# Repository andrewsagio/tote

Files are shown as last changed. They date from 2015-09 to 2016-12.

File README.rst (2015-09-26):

Tote, a Small Spider Quadruped Robot
************************************

This is a small (fits in your palm) walking robot, with three degree of freedom
legs, with Ardunio (Pro Mini) for the brain and controlled by a TV remote. It
is supposed to be very simple, very cheap and very sturdy (but please don't
step on it).

See the documentation at http://tote.rtfd.org

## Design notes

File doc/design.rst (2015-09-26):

Design Decisions
****************

Design Goals and Constraints
============================

The main goal is to have a walking robot that is interesting to program and at
the same time easy to build. From that, we get a number of constraints:

    * The robot has to fit on the desk, because not everyone has a garage.
    * It has to have inverse kinematics, otherwise we are limited to replaying
      pre-recorded movements.
    * It should avoid parts that are custom-made using tools and materials that
      are not widely available. In particular, no laser-cutting or 3D-printing.
    * The parts should be common, cheap and easy to get, also in bulk.
    * It should be possible to easily extend or modify the robot.
    * In the basic version it should have enough functionality to be fun to
      play with.

Hacks and Workarounds
=====================

Because of the above constraints and the desire to make it all as cheap as
possible, I've made some design decisions that are not exactly good
engineering.  I figured out that it's better to have a crappy but working
robot, than a beautifully designed plan. So here are some corners that I've
cut:

Mechanical Design
-----------------

The way this robot is assembled together only works because it's so
lightweight. Would the robot be heavier, there would be significant problems:

    * Servomotors are used as structural elements.
    * The printed circuit board is also used as a structural element.
    * The whole robot weight rests sideways on the servo shafts.
    * The servo horns used for legs are elastic.
    * The screws that come with the servos are too big for what they used for.
    * The servo cables are all over the place.
    * The power switch is in an awkward place.
    * There is no good way to attach the battery.
    * The legs need some rubber at their ends, or they will slip.

Most of those problems can be solved by using better materials and adding some
structural support elements, but that affects the price and complexity.

Electrical Design
-----------------

The desire to cut costs and minimise the number of parts also made me make some
not-entirely-kosher decisions on the electrical side of things:

    * The servomechanisms are under-powered. The specification asks for 4.6V,
      and they get from 3.6V to 4.2V depending on the charge level of the LiPo
      battery.
    * The servomechanisms are powered directly from the battery, without any
      kind of voltage regulator.
    * The undercharge battery protection is software-based, which means it can
      easily fail.
    * There is no battery charger build in. You have to disconnect the battery
      to charge it.
    * The Pro Mini is soldered directly onto the printed circuit board.

Those problems can be easily solved by adding the missing parts to the design.
There is even some room left for them, in the form of additional holes and
pins.

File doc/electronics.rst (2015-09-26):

Electronics
===========

The designs of the main printed circuit board are available in the code
repository_. You will need Fritzing software to open them and export as
whatever format is required for fabricating it.

.. _repository: https://bitbucket.org/thesheep/tote

Arduino Pro Mini is used for the brains of the robot. It is connected directly
to the servo signals and to the battery. There is also a 1000µF electrolytic
capacitor connected across the battery to avoid brown-outs. An optional voltage
divider of two 47kΩ resistors, with a 47nF capacitor for noise reduction is
used to monitor the battery voltage and shut down the robot when it drops too
low. The battery is any light 1S, 3.7V LiPo cell. Other kinds of batteries can
be used, as long as they are light enough and provide enough power. Remote
control is done using a VS1838B infra-red sensor, but other sensors can be
used.

Several pins of the Arduino are free, including the I²C pins, allowing for
connecting more sensors.

The prototype also has an optional LiPo charging/protection module attached,
for convenience, although the battery can be charged by any suitable charger.

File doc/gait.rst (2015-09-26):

Walking Algorithms
******************

The way in which an animal or a robot walk is called a gait -- it tells us
how and in what order the legs are moved, how the body is balanced and how
it moves forward.

Statically and Dynamically Stable Gaits
=======================================

When the robot walks, it has to keep its balance. There are two general
strategies for doing that, and according to them, we divide the gaits into
statically stable and dynamically stable.

For statically stable gaits it doesn't matter how fast they are performed, or
whether the robot is stopped in a middle of a step -- it is stable at any
moment, at all times. Animals and people use those gaits when they want to go
slowly, or when they want to be able to stop at any time. An example of such a
gait is the "creep" gait, used by cats stalking their prey.

Dynamically stable gaits are much harder, as they have to be performed at a
particular speed and cannot be interrupted at an arbitrary point. They are
sometimes called "controlled falling", as they exploit the fact that it takes
some time for the robot to fall when it's unstable, and that time can be used
to move the legs in such a way as to prevent the fall. Most animal gaits are
dynamically stable, as they tend to be faster and more energy-efficient. An
example of a simple dynamically stable gait is the "trot" gait.

Area of Support
===============

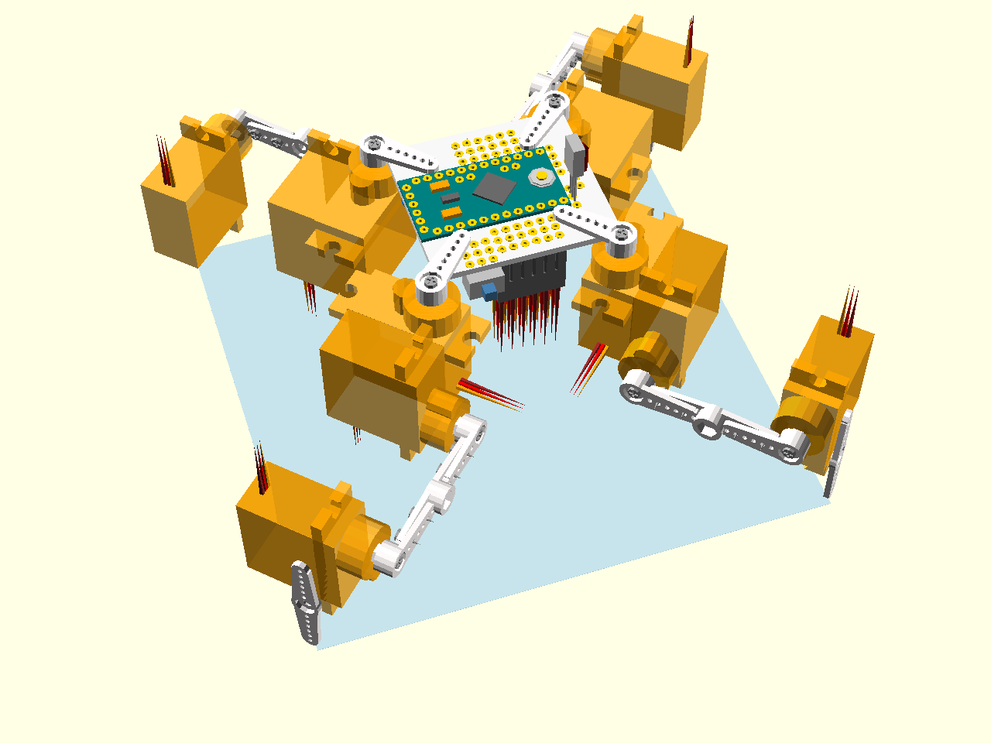
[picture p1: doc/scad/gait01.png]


I order for a relatively light robot, like ours, to be statically stable, it
has to keep its center of mass somewhere between its legs. More precisely, if
you connect all the feet on the ground with straight lines, so that they form a
convex polygon, the center of mass has to be located directly over it. We call
that polygon the "area of support" of the robot at the given moment. The area
of support will change depending on which legs are placed on the ground and
where, so the robot will sometimes need to shift its center of mass around to
remain stable while changing its stance.

The image above shows the are of support of our robot in the starting position.

In a heavier robot, you also have to take into account the inertia, so that
it's not sufficient to just track the center of mass -- you have to track the
so-called "zero-moment point", often abbreviated ZMP, which is basically the
point on the ground directly below the center of mass, shifted to account for
the inertia. We will not get into details of that here, as our robot is light
enough that just leaving some small margin around the area of support is
enough.

Raising a Leg
-------------

When the robot raises one of the legs, its area of support changes dramatically:

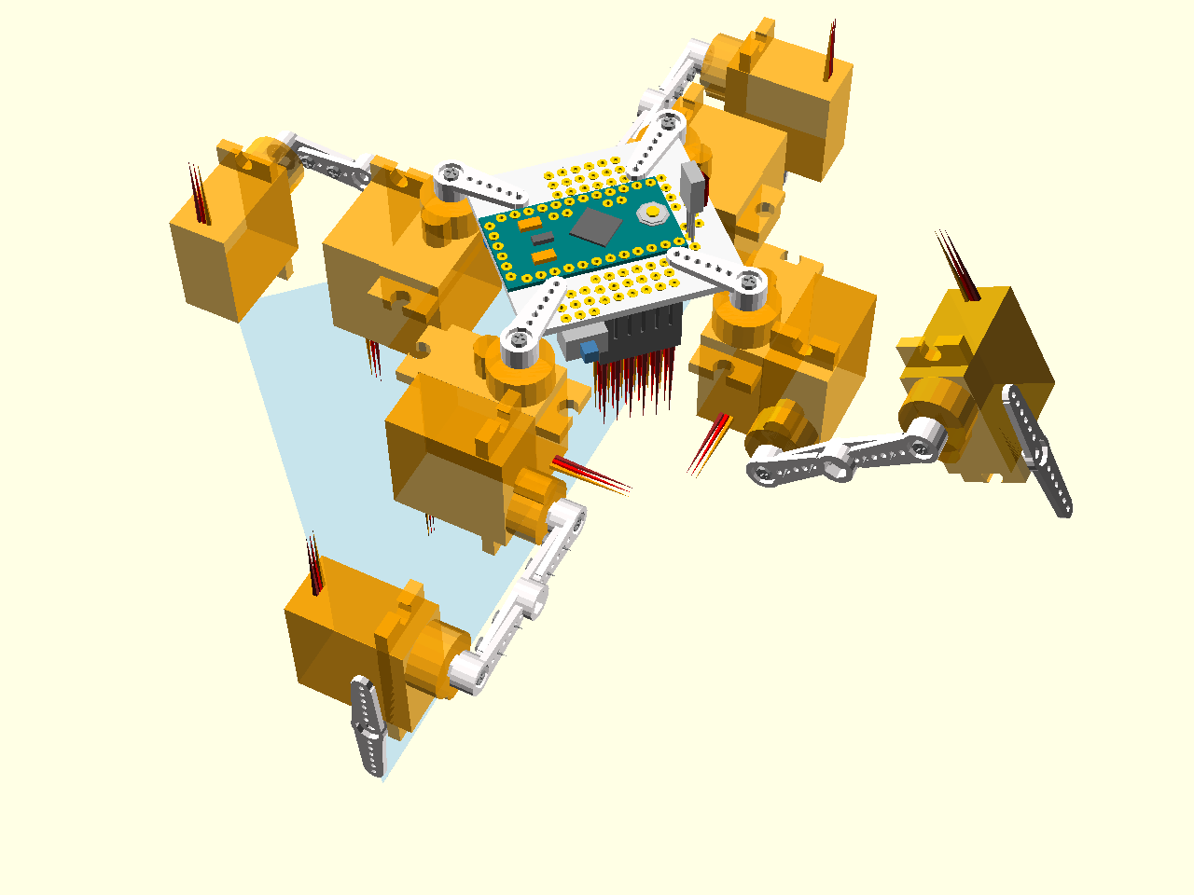
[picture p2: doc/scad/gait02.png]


You can see, that our center of mass is directly on an edge of our area of support. That's bad, because the smallest force can now tip our robot and make it fall. We can avoid that by moving all the legs toward the one leg that we want to raise before raising it, so that the center of mass shifts:

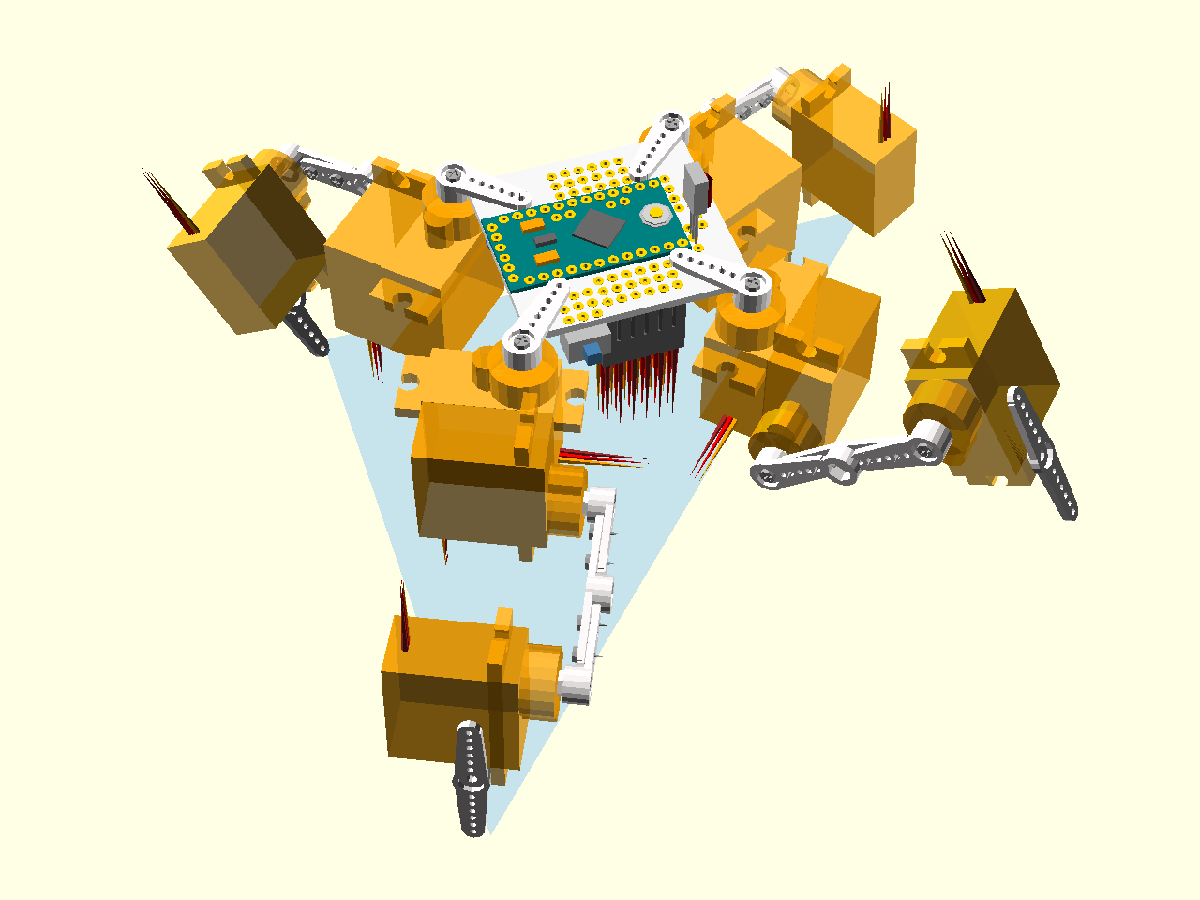
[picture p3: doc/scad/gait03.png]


There are also other methods of balancing, not covered here. For example, many
animals have a flexible spine, that they can bend sideways to shift their
center of mass. Other animals have tails that they use to balance.
Possibilities are endless.

Moving Forward
==============

Our goal is to propel our robot horizontally across the floor. The simplest
solution to do that, at least initially, is to just move all the legs that are
touching the ground backwards. If we do it slow enough, so that they don't
slip, they will stay where they were, but move the body of the robot forward.
This is an excellent way of moving around, and many industrial robots do it
this way, bolted to the floor in one place. There is however a small problem:
the range is quite limited. Sooner or later you will either move your center of
mass outside the support area, or your legs move to their maximum range. What
then?

Then you raise the legs from the ground, move them forward, and set them down
in the new place. But you have to be smart about it, because if you do it with
all the legs at once, you will fall down. But you can raise a single leg and
still stand on the remaining three. You can also raise and move that leg
*while* moving the remaining legs backwards, which saves you some time and
makes it both faster and more smooth.

Now, as you know, if you are raising a leg, you also have to make sure that the
center of mass stays inside the support area. To do that, you will have to
shift the robot's body away from the leg that you are rising. Since you are
shifting your body forwards, it is also important in which order you raise the
legs -- some orders will be more stable than others.

So, to sum, our plan of action is:
  * move all the legs that are on the ground backwards,
  * for each leg in a set order:

    + shift the body away from that leg
    + raise the leg
    + move the leg forward
    + set the leg on the ground.

The Creep Gait
==============

What order is the best for making steps, if you raise one leg at a time? There
are four possible orders, assuming you always start with the same leg, and
ignore the orders that are just reflections.

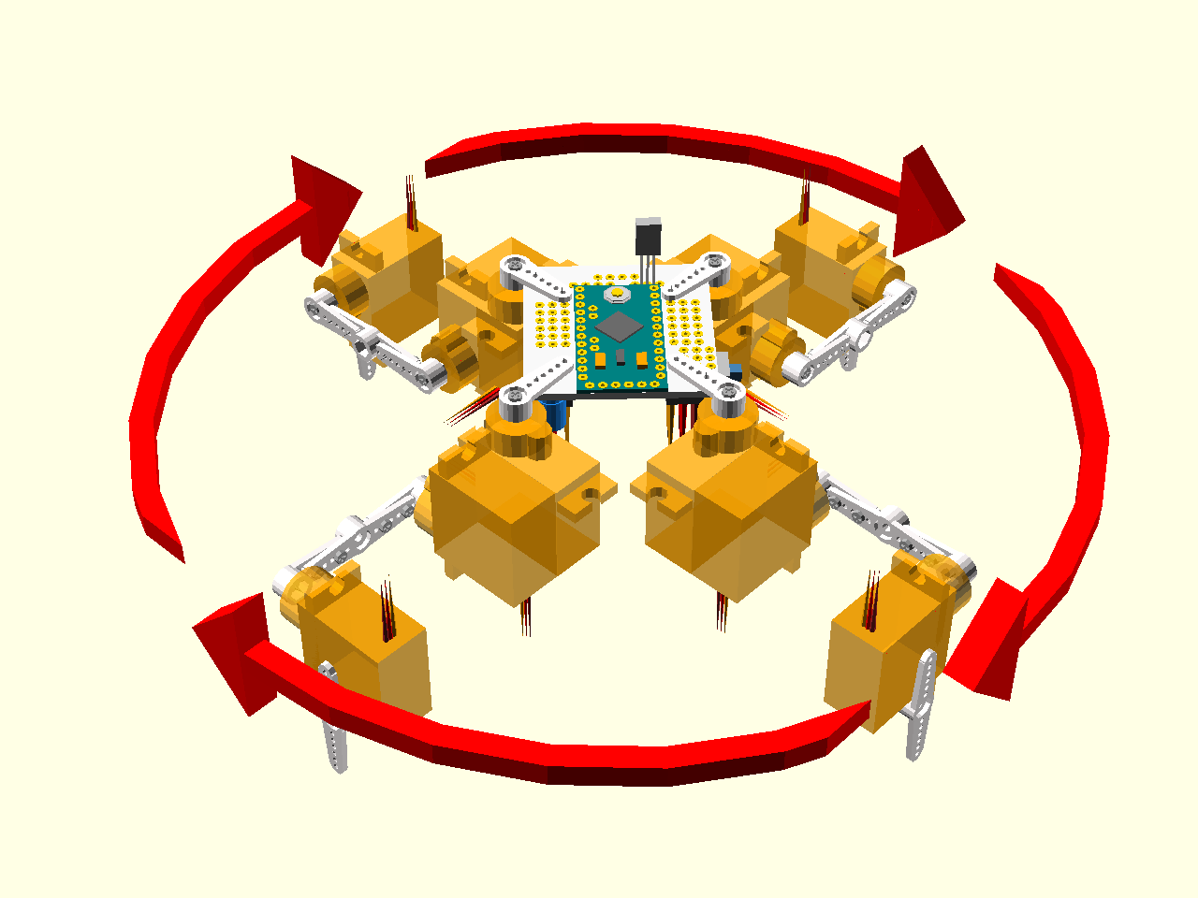
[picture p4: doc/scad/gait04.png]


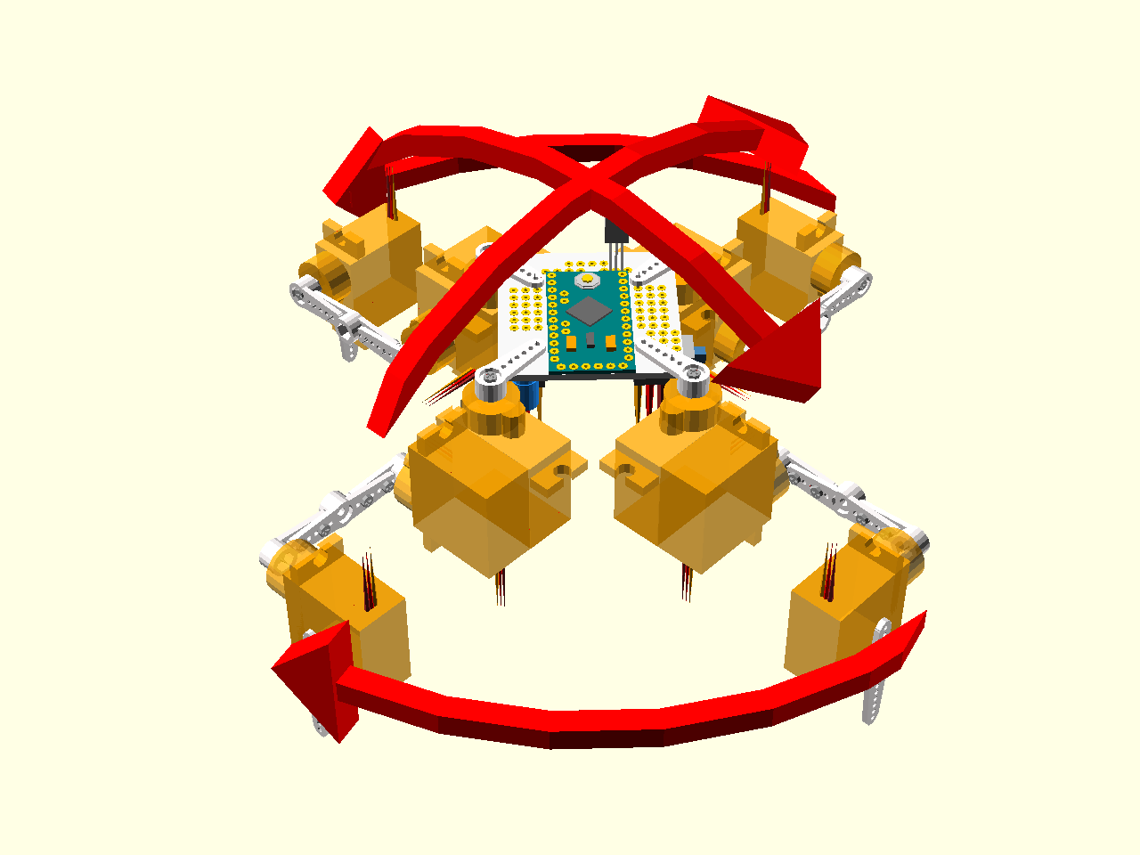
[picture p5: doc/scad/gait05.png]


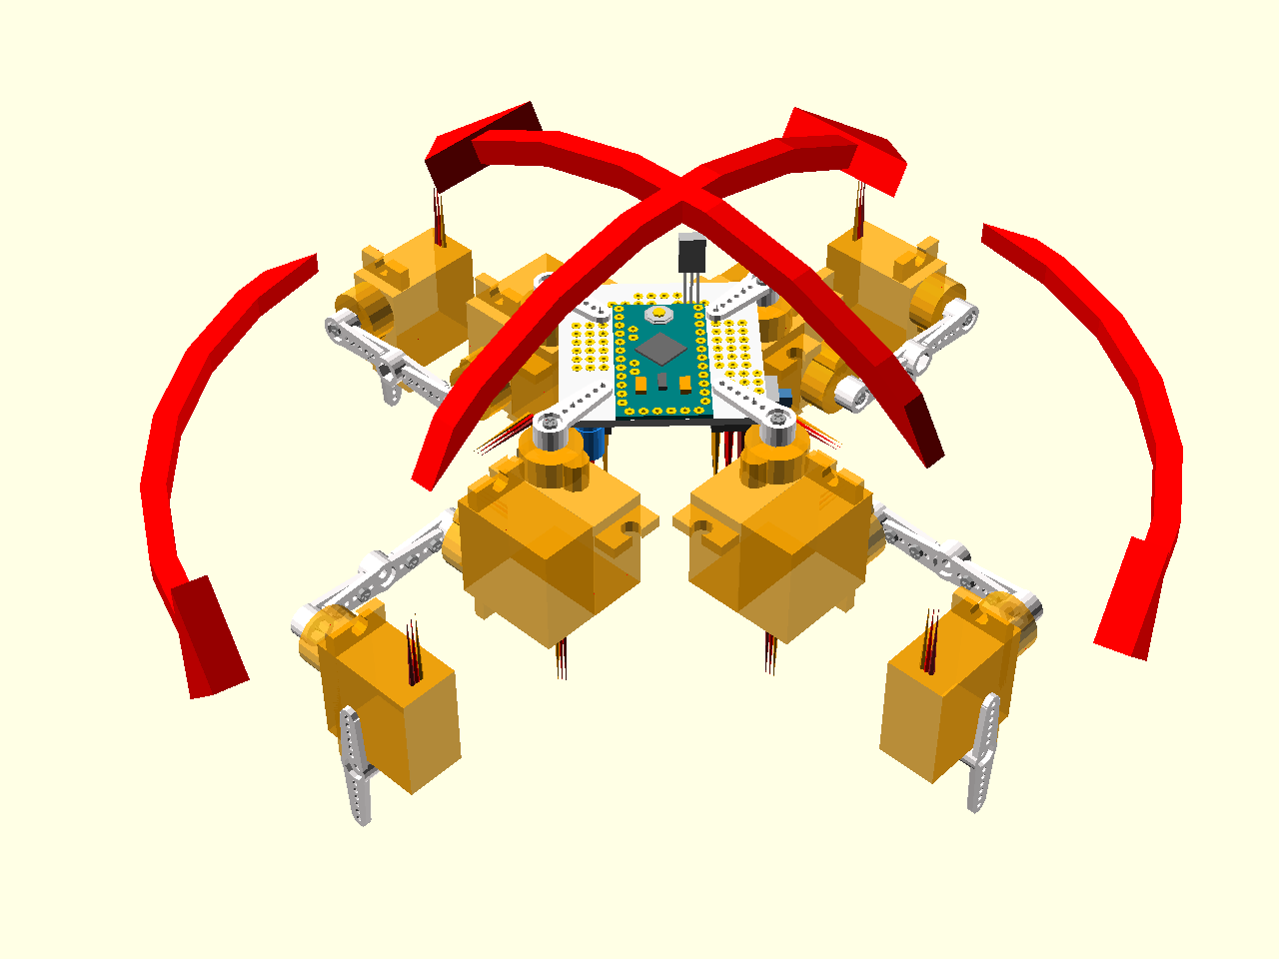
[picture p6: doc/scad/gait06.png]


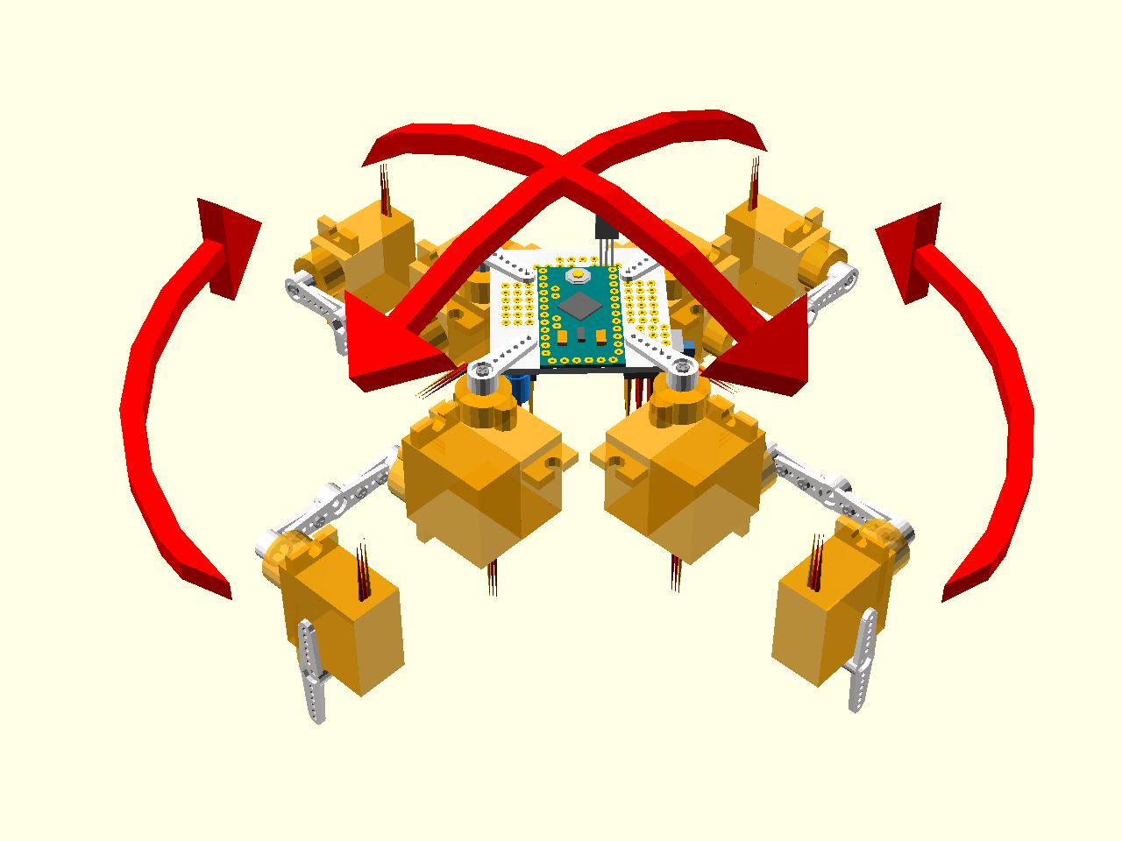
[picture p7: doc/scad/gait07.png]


Both calculations and experimental data show that the last one, a figure eight
orthogonal to the direction of walking, provides the optimal stability at all
moments.  Note that this order is best only when you are moving forward. If you
are moving sideways, backwards or rotating, then other leg orders are optimal.
That's why it probably makes sense to adapt the order to the situation.

The Trot Gait
=============

The creep gait is stable, but quite slow -- raising only one leg at a time, you
can't move the remaining legs backwards too fast, or you move out of the range
of your legs. In addition, shifting the robot's body before each step also
takes some time. Is there a faster way?

Turns out that you can move two opposite legs at the same time, if only you do
it fast enough, so that the robot will not have time to tip on the two
remaining legs. This is not a statically stable gait -- you can only stop
safely between steps, when all the legs are on the ground, but it's more than
twice as fast as the creep gait: first, you move two legs at a time, and
second, you don't have to shift your body for balance.

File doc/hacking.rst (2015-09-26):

Modifying and Extending
***********************

Since this robot is so simple, it is very easy to modify or extend it. You can
add sensors and peripherals, or control it remotely from another computer or
directly with another microcontroller or microcomputer board.

GPIO Pins
---------

Most of the Arduino's pins are used internally, but there are several of them
left for your use:

  * 7 pins can be used as digital,

    - 1 of them has a LED on it,
    - 2 of them can be used as serial interface,
    - 2 of them can trigger interrupts,

      + 1 of them has PWM,

    - 2 other can be also used as analog pins,

      + they can also be used as I²C interface,

  * 2 analog-only pins.

Sensors
-------

You can connect anything that runs on 3.3V and can be connected either to the
free GPIO pins, or to additional board or multiplexer that you add. Examples
include:

  * ultrasonic distance sensor, such as HC-SR04,
  * switches at the ends of the feet,
  * accelerometer, gyroscope and/or compass,
  * encoders for leg positions,
  * light sensors, for following light,

Peripherals
-----------

You can also use the GPIOs to attach additional hardware that would do
something. Unfortunately, you cannot easily add more servos, as the Arduino
Servo library being used only supports 12 of them at once. But instead you
can add:

  * piezoelectric buzzer, for beeping,
  * addressable LEDs, for light effects,
  * infrared diode, for "shooting" at other robots in a laser-tag game,
  * a nerf gun,
  * a LiPo battery charger.

Remote Control
--------------

You can use the serial interface to connect a transmitter/receiver module and
make the robot communicate with another device. For example, you can use:

  * WiFi module, such as ESP8266,
  * Bluetooth module, such as HC-05,
  * Radio module, such as NRF24,
  * BLE module,
  * and so on.

Additional Boards
-----------------

You can also add another microcontroller or microcomputer board to the robot,
and make it communicate with it either through the serial or I²C pins. Some
examples include:

  * Arduino Pro Mini, with more pins,
  * VoCore, a computer running OpenWRT Linux,
  * PyBoard, a microcontroller runnning MicroPython,
  * Teensy 3.1, an ARM-based microcontroller board,
  * OpenMV, a microcomputer with a camera, programmable with Python,
  * ESP8266 with NodeMCU firmware, programmable in Lua.

The possibilities are infinite, as long as the board in question has a serial
or I²C interface, can be powered from a single LiPo battery, and doesn't weight
too much for the robot to carry it.

If your board or module can be powered with 3.3V, simply use the FTDI header of
your Pro Mini for connecting it -- it has broken out the power and serial
interface. You will have to write the code for communicating with the board
yourself.

If the board requires 5V or considerable amounts of current, you don't want to
power it from Pro Mini's power regulator. Instead, add pins to the RAW and GND
pads on it, and to the RX and TX pads:

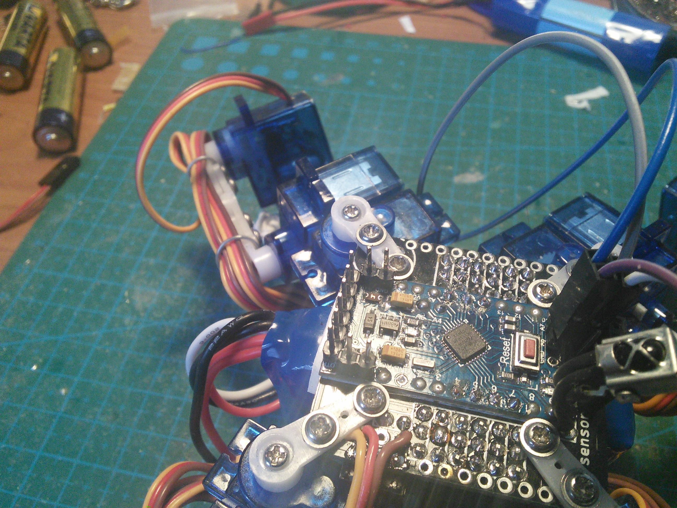
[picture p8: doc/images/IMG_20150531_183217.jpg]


Then use a double-row female header to connect your breakout board to the Pro
Mini:

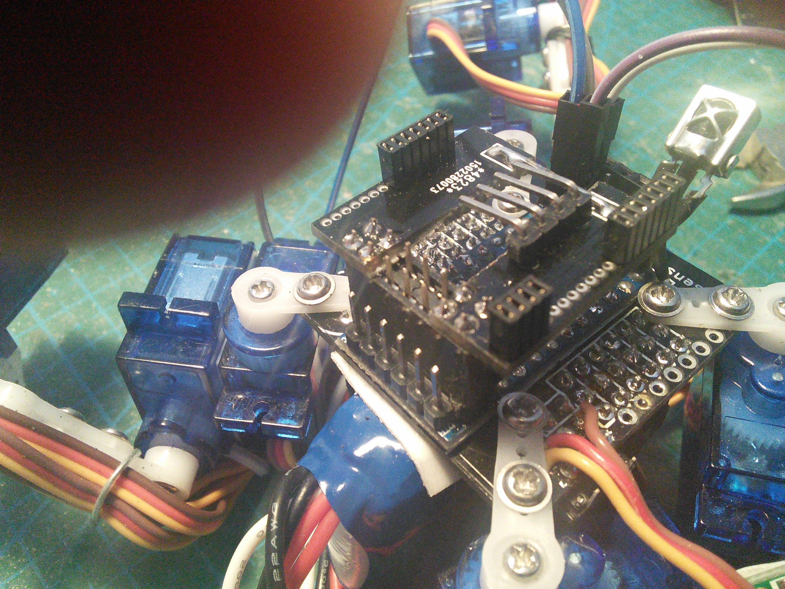
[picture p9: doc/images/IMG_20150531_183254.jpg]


And connect your board on top of that:

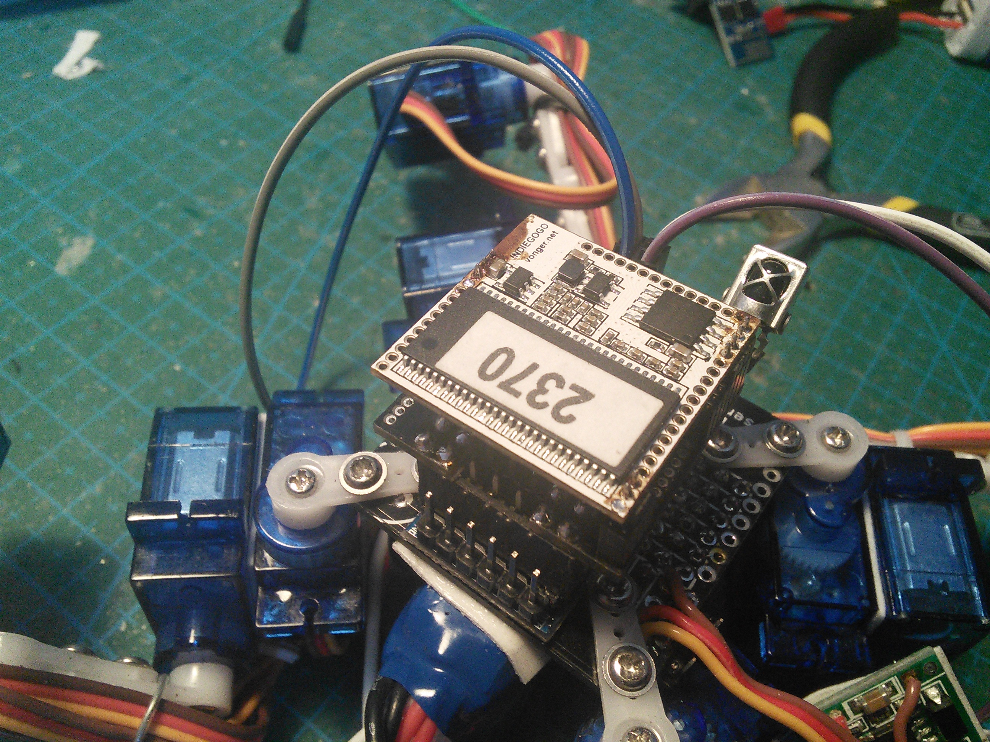
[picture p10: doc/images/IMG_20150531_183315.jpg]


Of course, you will need to use a power source that can power your board.

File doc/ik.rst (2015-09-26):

Inverse Kinematics
******************

Kinematics is the process of determining how a robot will move given certain
inputs. Inverse kinematics is for determining what inputs we need to give it to
get into a certain position. In particular, leg inverse kinematics for walking
robots is the process of calculating the angles for all the joints required to
get the tip of the leg in a certain position relative to the body. There is
also body inverse kinematics, which tells us in what positions the legs have to
be for the body to be in a certain position (tilt, yaw, rotation, shift).

This are notes for determining the inverse kinematics for a four-legged robot
with three degrees of freedom per leg. Let's start with an image of the leg:

Basic Trigonometry
==================

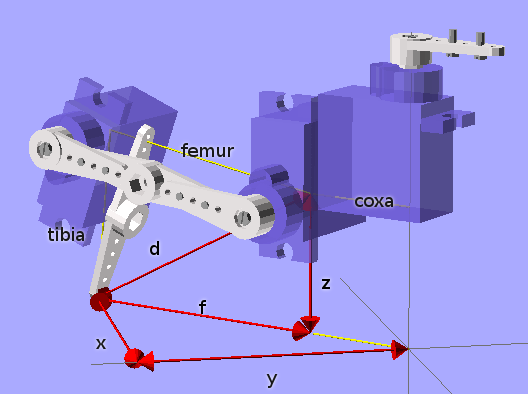
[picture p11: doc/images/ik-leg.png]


For a start, need to determine the geometry of the leg and describe it using
mathematical formulas. For that, we will start with a few tricks from the
elementary school.

To calculate the diagonal of a rectangle, we can use the Pitagoras theorem,
:math:`c^2=a^2+b^2`, so :math:`c = \sqrt{a^2+b^2}`.

To calculate one of the angles of a triangle for which we have the lengths of
all sides, we can use the Law of Cosines: :math:`c^2 = a^2 + b^2 -
2ab\cos{\alpha}`, which gives us :math:`\alpha = \arccos{a^2 + b^2 - c^2 \over
2ab}`.

Finally, to calculate the angle of the diagonal in a rectangle, we have :math:`\beta
= \arctan{{y\over x}}``, or better, ``beta = atan2(y, x)``, as most languages
have a convenience function for this that also handles the sign properly.

Solving a Leg
=============

We are given the coordinates :math:`(x, y, z)` and we want to calculate the
angles :math:`(\alpha, \beta, \gamma)` of the hip, knee and ankle joints. We
also have the lengths of coxa (:math:`L_c`), femur (:math:`L_f`) and tibia
(:math:`L_t`).  The hip is easy:

.. math::
    \alpha = \mathrm{atan2}(y, x)

All the rest is happening in one vertical surface along the hip angle, so we
can convert our :math:`(x, y, z)` into :math:`(f, z)`, where :math:`f =
\sqrt{x^2 + y^2} - L_c` is the part of the diagonal starting at the knee joint
(see picture).

The knee angle is going to consist of two parts. The first is easy,
:math:`\beta_1 = \mathrm{atan2}(z, f)`. For the second, we need to know the
lenght of the diagonal :math:`d = \sqrt{f^2 + x^2}`. Once we have :math:`d`, we
can solve the triangle formed by tibia and femur, and we get :math:`\beta_2 =
\arccos{L_f^2 + d^2 - L_t^2 \over 2L_fd}`. Finally:

.. math::
    \beta = \beta_1 + \beta_2

Solving the same triangle, but for a different angle, will give us our ankle
angle:

.. math::
    \gamma = \arccos{L_f^2 + L_t^2 - d^2 \over 2L_fL_t}

Trim and Reverse
================

We have the angles, but they are unlikely to have to align with where our
physical servomotors have their zero angles, and the direction they turn. So we
have to add some offsets to them, and possibly reverse them. The easiest way to
go about that is to set all your servos to 0 and check where the end of the leg
should be then. Then run those coordinates through our formulas, and you will
get the numbers that you have to subtract from our calculated angles (so that
at the initial position they are all zero). Then move them a little from the
initial position and see if the directions are right.

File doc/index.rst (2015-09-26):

.. Documentation master file, created by
   sphinx-quickstart on Sat Feb 21 16:36:41 2015.
   You can adapt this file completely to your liking, but it should at least
   contain the root `toctree` directive.

Tote -- Quadruped Robot
=======================

Tote is a small (fits inside your palm), four-legged, walking robot, with three
degrees of freedom per leg, Arduino for its brains and controlled either with a
TV remote, or by additional electronics added on top of it. It is very simple,
cheap and sturdy, for this class of robots. Its goal is to be a starting point
for anyone who wants to start building multi-legged robots.

.. raw:: html

    <iframe width="560" height="315"
    src="https://www.youtube.com/embed/XXotn-8DPQo" frameborder="0"
    allowfullscreen></iframe>

Contents:

.. toctree::
   :maxdepth: 2

   intro.rst
   bom.rst
   tools.rst
   assembly_v2.rst
   assembly_v4.rst
   electronics.rst
   software.rst
   hacking.rst
   design.rst
   ik.rst
   gait.rst
   tutorial.rst
   help.rst

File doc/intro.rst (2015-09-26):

Introduction
************

What is Tote?
=============

It's a small walking robot, designed to be as cheap and simple to build as
possible, while at the same time serving as a starting point for more complex
projects and for teaching. In its basic form it just walks around and turns,
controlled by a TV remote, but it can be easily extended by adding sensors and
more interesting behaviors.

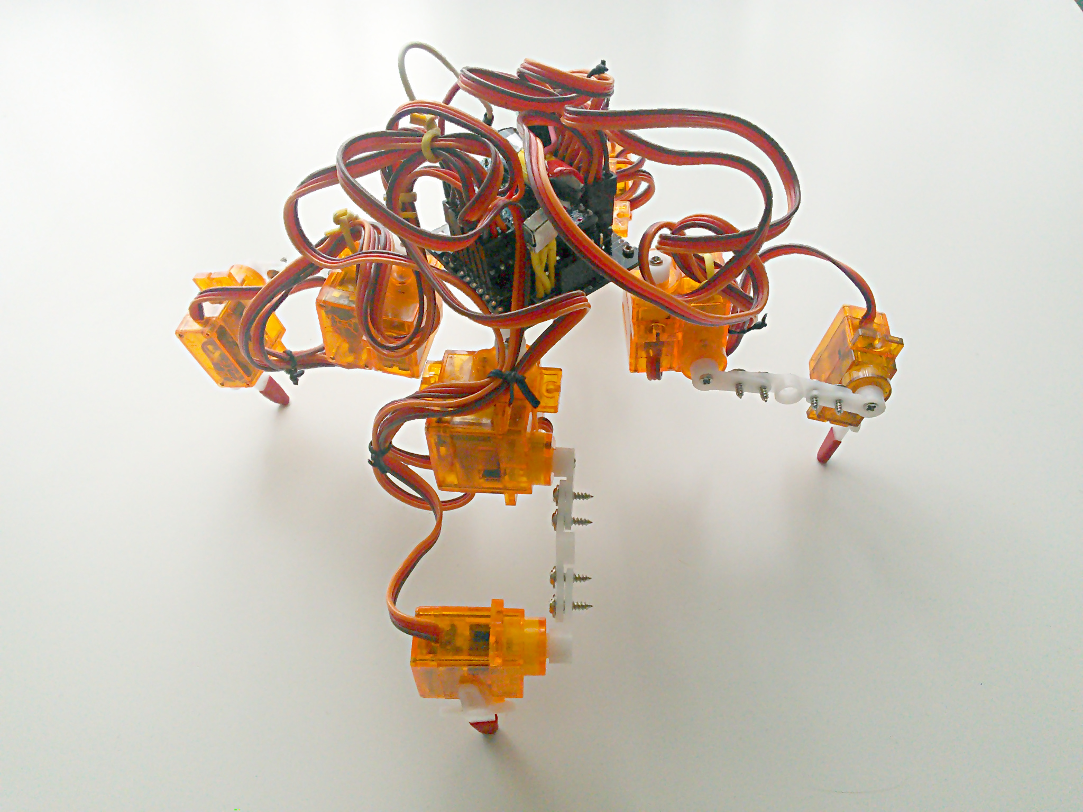
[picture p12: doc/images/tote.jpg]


How is it different from all those toys?
========================================

Most walking toys available currently are not very different from the wind-up
toys that our parents used to play with -- except they have an electric motor
instead of a spring. But the whole walking pattern is hard-wired in the
mechanism of the toy, and it can do nothing more than walking forward and
backwards on flat surfaces, and maybe turning.

This robot is potentially more than a toy. While the basic functionality that
you begin with is pretty much the same, this robot can move each of the legs
individually within three degrees of freedom, controlled with a computer
program that you can freely modify. You can make it dance, you can make it
climb, you can make it follow any movement plan. Furthermore, you can add
sensors and modules to it, that would allow you to make it do practically
anything -- as long as you have enough skill to actually program it. Don't get
me wrong, it's very hard to make it do even the simplest things -- but the
point is that you can!

Challenges
==========

A lot of walking robot projects never get very far, because they turn out to be
much more complex, expensive and fragile than initially anticipated. By making
certain choices about size, materials and software, I managed to keep Tote
relatively simple, affordable and robust. Thanks to its small size it has more
than enough power to carry its weight, and the simple plastic parts are enough
to hold it together and even survive falls from heights with just minor damage.
At the same time, being just a starting point, Tote gives you a lot of room for
improvement and experimenting.

Required Skills
===============

First and foremost, you will need patience. A lot of decisions were made here
trading time for money. You will wait for the printed circuit board to be made
for you in a factory and then shipped to you. You will wait for shipment of all
the parts you order online. Once it all arrives, you will spend hours debugging
and fine-tuning the code. So this is not a project for aggressive deadlines.

You will also need to glue things together and assemble them using screws. You
will probably also need to use a file to adjust parts that don't quite fit. You
won't need a mechanical saw or drill, though (assuming you use a PCB they made
for you in a factory -- if you are hardcore, you can make the PCB yourself).

This project requires some basic soldering -- at the level of soldering pin
headers to a module, or soldering wires to a PCB. Be careful not to burn
yourself.

You will have to properly connect the USB2TTL converter to your robot to
program it from your computer using the Arduino IDE. For basics you don't need
to know how to code, as all the code is written for you, but you will probably
want to modify and extend it once you get it to work.

Depending on how proficient you are in such things, it can take you anywhere
from four to eight hours to get it all working.

In order to take the project further, you will need at least basic knowledge of
Arduino programming and information about how the sensors that you want to use
work, and how to manipulate the data that you receive from them. If you add
more modules, you will also need to know how to program those. This is a huge
topic, and you can keep learning and experimenting for years.

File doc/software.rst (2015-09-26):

Software
********

Tote comes with example program, that makes it walk forward, and lets you
control it with a TV remote. If you want to control it from a PC or a different
board, then you will have to write your own software.

All the required code is included in the repository_. You will need an Arduino
IDE and a TTL2USB programmer for the Pro Mini to compile and upload the
software into the robot. Connect the programmer, open ``start.ino`` in the
Arduino IDE, and click "Upload". That's all.

.. _repository: https://bitbucket.org/thesheep/tote

For the infra-red communication, I'm using the excellent IRLRemote library,
written by NicoHood. You may want to adjust the ``ir.ino`` file to modify the
button commands and the protocol, so that they match your TV remote.

Features
========

Creep Gait
----------

Right after switching on, the robot will start walking forward using the creep
gait. This is so that you can see that it works properly even when you don't
have a TV remote at hand.

Remote Control
--------------

You can use a TV remote to control the robot. Direction keys will make it speed
up/slow down, go backwards or turn. You can also raise and lower its body,
spread the legs more, make it go sideways, etc.

Power Off
---------

The power button on the TV remote will make it fold and shut down -- the servos
will be powered down and the board will enter a sleep mode. You should switch
it off with the power switch manually anyways, because it will still consume
some power in that state.

Battery Monitoring
------------------

If the battery voltage drops too low (and you have soldered the optional two
resistors and a capacitor required for monitoring it), it will also fold and
switch off when the battery voltage runs too low. Note, that it will probably
not have enough power to finish folding in this situation, so it may end up in
an awkward position, or even in a restart loop. You should switch it off and
charge the battery as soon as possible.

Trot Gait
---------

Pressing the direction buttons multiple times makes it walk faster by making
longer steps, until it can't go faster anymore, and then it will switch to a
trot gait, which is about two times faster, but unstable.

Automatic Leg Order
-------------------

The order in which the legs make steps is important for stability. The robot
will automatically select the optimal leg order depending on the direction in
which it is moving.

Beeper
------

If you connect a piezo buzzer to pin 13 and ground, you can make this robot
beep with every step and when it receives a command. This is muted by default
and has to be enabled with a button on the remote, because it's so annoying.

Modes
-----

You switch the modes of operation of the robot with a button on the remote.
Initially there are only two modes: walking and doing nothing. You can easily
add your own modes for additional functions that you program.

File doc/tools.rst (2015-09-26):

Required Tools
**************

You will need:
 * soldering iron and some solder,
 * USB2TTL module, with cables,
 * cyano-acrylic glue, or other glue suitable for gluing plastic,
 * small Phillips screwdriver,
 * metal file,
 * TV remote.

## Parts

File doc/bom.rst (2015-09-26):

Bill of Materials
*****************

With the exception of the printed circuit board, which you have to make or
order according to the provided designs, all parts are off-the-shelf, ready
to use components which you can find in hobby stores, or even better, order
online.

Required
========
   * Printed Circuit Board, the board design file is in the repository,
   * Arduino Pro Mini, 3.3V/8Mhz version,
   * 12 SG90 Micro Servos, with screws and plastic horns,
   * 2.54mm pin headers, with at least 38 pins total,
   * 3.7V 1S LiPo Battery (I used a 300mAh battery),

Optional
========
   * Infra-Red Receiver (I used VS1838B).
   * Ultra Sound distance sensor (I used HC-SR04),
   * 1000µF electrolytic capacitor, for avoiding brown-outs,
   * 2 47kΩ SMD resistors and a 47nF SMD capacitor, for battery monitoring,
   * Power Switch, for convenient on/off without unplugging the battery,
   * Piezoelectric Buzzer, for making noises,
   * Battery Charger Module, for charging the battery without unplugging,
   * Small Rubber Hose, for the feet,
   * Any additional sensors or boards you require.

At the time of writing, the required materials could be bought online for about
$50 total, but it greatly depends on availability, amount, and quality you
require. Also, consider the shipping time, especially for the parts ordered
overseas.

Printed Circuit Board
=====================

This is the only custom-made part of the robot. It's used to connect all the
parts electrically and hold them together mechanically. The design files for
the board are available in the repository_ in form of files for the Fritzing_
program. You can use that program to open the files, optionally make any
changes you want, and export them to whatever format you require. Then you can
send your designs to a prototype board fabrication service and have them
created for you.

If you don't have an access to a prototype board fabrication service, or don't
want to use it, you can also create the board yourself, or even use a
perma-board and make the connections with pieces of wire. This is not covered
in this instruction, however.

.. _repository: https://bitbucket.org/thesheep/tote
.. _Fritzing: http://fritzing.org

**Shameless plug.** You can order the board from Dirty PCBs here: `order the
board`_. If you do so, I will get a $1. You can also order the board anywhere
else, using those `gerber files`_.

.. _`order the board`: http://dirtypcbs.com/view.php?share=6918&accesskey=97f6a684899c11fcc50da07808869f5d
.. _`gerber files`: https://bitbucket.org/thesheep/tote/src/tip/fritzing/pcb4.zip

Arduino Pro Mini
================

The Arduino Pro Mini, or any of the widely available Pro Mini clones, are the
cheapest Arduino boards available, even as cheap as $2 a piece. That price is
achieved by stripping them of anything that isn't necessary -- including the
USB port. You cannot connect this board directly to your computer for
programming, as you can other Arduinos, instead you have to use a device called
``USB2TTL``. But you only need one such device, and you can re-use it for
programming as many Pro Minis, as you want.

You can also use a different small Arduino board, such as Nano or Pro Micro,
but that will require adapting the pin numbers, though.  They do have an USB
port on them, which will stick a little bit out from the back of the robot.

It's very important that you use a 3.3V version of the board. There are two
versions, 5V and 3.3V, which differ in what voltage they expect. If you get the
5V version, it won't run on the single LiPo battery that we are using here.

The Pro Mini usually comes with three unsoldered pin headers, as you can see
here:

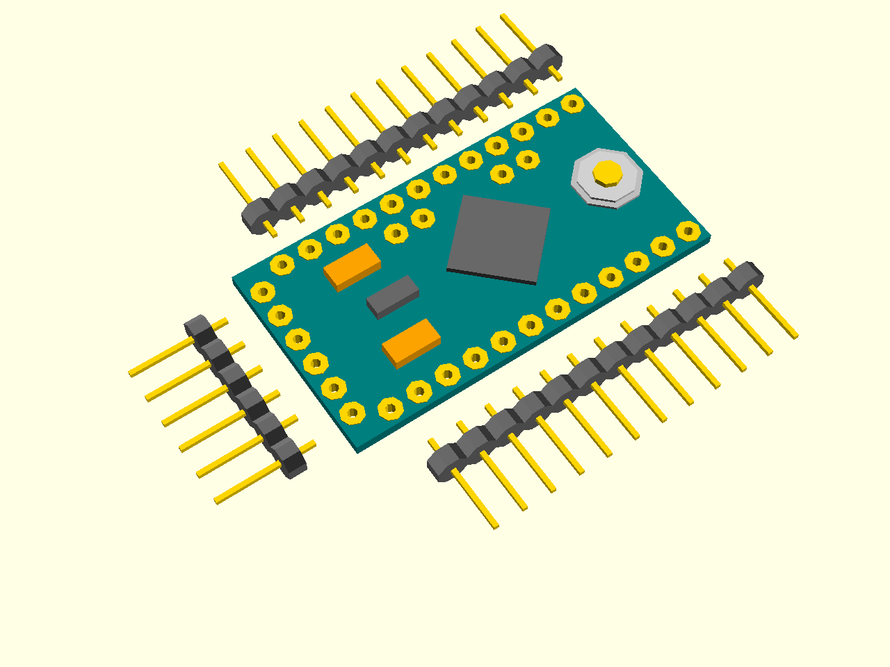
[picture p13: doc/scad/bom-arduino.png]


You will need to solder at least the short, 6-pin one (it may be a little
different version, with pins angled at 90°, but it doesn't matter much).
Remember to make it stick out at the top of the board, on the same side as all
the components, and leave the empty side of the board flat. Those are the pins
that you will use to program and debug your robot.

If you want to use sockets, you can also solder the two longer pin headers --
those come on the bottom of the board, on the empty side. If you don't want the
board to be removable from your robot, you can skip those and use them for the
servo sockets instead.

SG90 Micro Servos
=================

Those micro servomechanisms are commonly used in radio-controlled toys and
models, which makes them easily available and cheap. We will need 12 of them,
so the price is really important here. The specific SG90 model was chosen
because it's the cheapest currently available. You can replace it with any
other nine gram servomechanism instead.

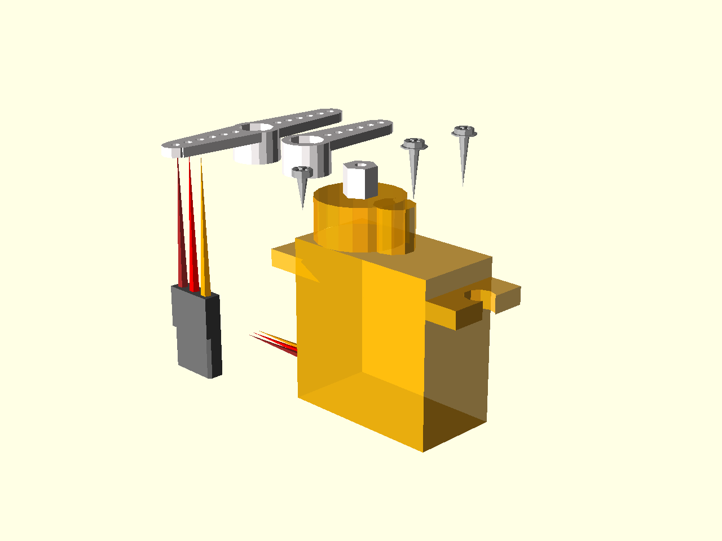
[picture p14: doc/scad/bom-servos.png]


Each servo comes with a set of plastic horns (single, double and cross-shaped),
as well with three screws (one small and two larger). We will need those to
build our robot's legs. This way you don't need any additional mechanical
parts.

Be careful when you are moving the servos by hand, they are not designed for
that and it's very easy to break one of the plastic gears inside them doing
that. Such a "stripped" servo is useless for our needs and has to be replaced.

Pin Headers
===========

Those are the same as the ones you get with the Pro Mini. In fact, if you are
not using sockets, you can use them. But that's only 24 pins, and you will need
a total of 38 pins, so you need to get more. You can buy them easily at any
electronics parts shop. Don't worry about their exact lengths, you will break
them into the lengths that you need.

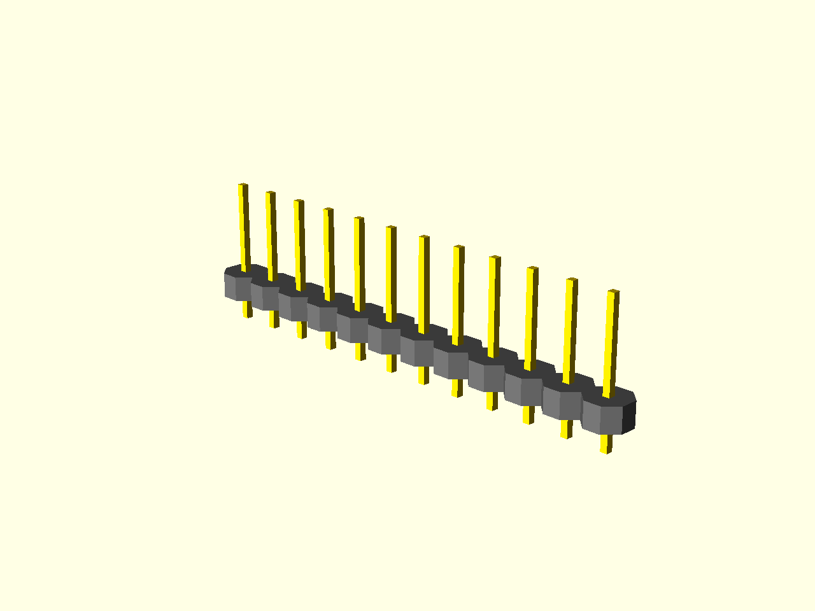
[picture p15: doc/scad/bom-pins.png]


1S LiPo Battery
===============

Your robot will need some kind of power source. We can't use regular batteries
(alkaline or rechargeable), because they are way too heavy for our robot.
Remember, that the robot has to be able to carry its own weight on those legs.
That's why we will use a much lighter LiPo battery. You should be able to buy
one easily in an electronics parts shop, a hobby remote-control models shop, or
you can even use an battery from an old cellphone. Just make sure it's small
and light and has only one cell, that is, has voltage of 3.7V.

Be careful when handling such batteries. Unlike the regular alkaline batteries,
they are very sensitive to mishandling. Damaging them mechanically,
overcharging or even short-circuiting them can make them explode and release
toxic chemicals.

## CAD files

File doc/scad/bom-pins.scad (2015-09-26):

use <parts.scad>;

for (pin = [-6:5]) {
    translate([0, 2.54 * pin, 0]) goldpin();
}

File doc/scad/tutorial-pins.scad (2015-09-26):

use <parts.scad>;

arduino_pro_mini();
translate([2.54, 2.54 * 12.5, 0]) for (pin = [0:5]) {
    translate([2.54 * pin, 0, 0]) goldpin();
}

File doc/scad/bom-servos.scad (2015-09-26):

use <parts.scad>;

SG90();
translate([-10, 0, 0]) SG90_horn_screw();
translate([20, 0, 0]) SG90_mount_screw();
translate([10, 0, 0]) SG90_mount_screw();
translate([0, 10, 0]) SG90_single_horn();
translate([0, 20, 0]) SG90_double_horn();
translate([-10, 20, -30]) rc_servo_plug();

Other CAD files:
doc/scad/gait01.scad
doc/scad/assembly01.scad
doc/scad/assembly01b.scad
doc/scad/assembly02.scad
doc/scad/assembly03.scad
doc/scad/assembly04.scad
doc/scad/bom-arduino.scad
doc/scad/gait02.scad
doc/scad/gait03.scad
doc/scad/gait04.scad
doc/scad/gait05.scad
doc/scad/gait06.scad
doc/scad/gait07.scad
doc/scad/parts.scad
doc/scad/pkubik.scad
doc/scad/tote.scad
doc/scad/tutorial-solder.scad

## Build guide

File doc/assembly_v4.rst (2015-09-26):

Assembly Instructions for PCB Version 4
***************************************

Decide on the Version
=====================

There are two ways to assemble the board:

You can put everything on top of the board, with the microcontroller board
plugged into a set of female headers like this:

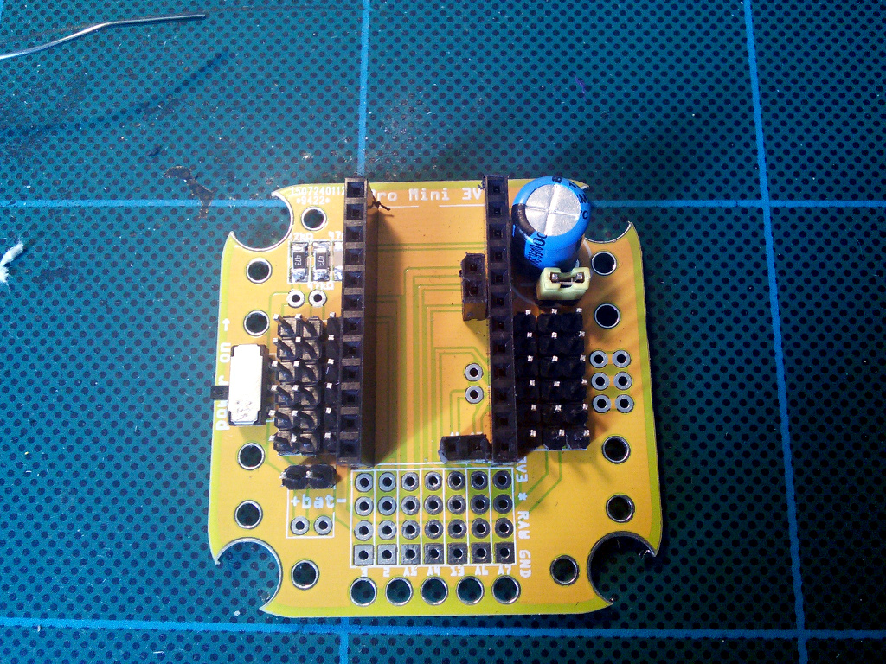
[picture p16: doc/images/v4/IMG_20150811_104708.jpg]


Or you can have the microcontroller board permanently attached on top of the
robot, and most of the components on the bottom side:

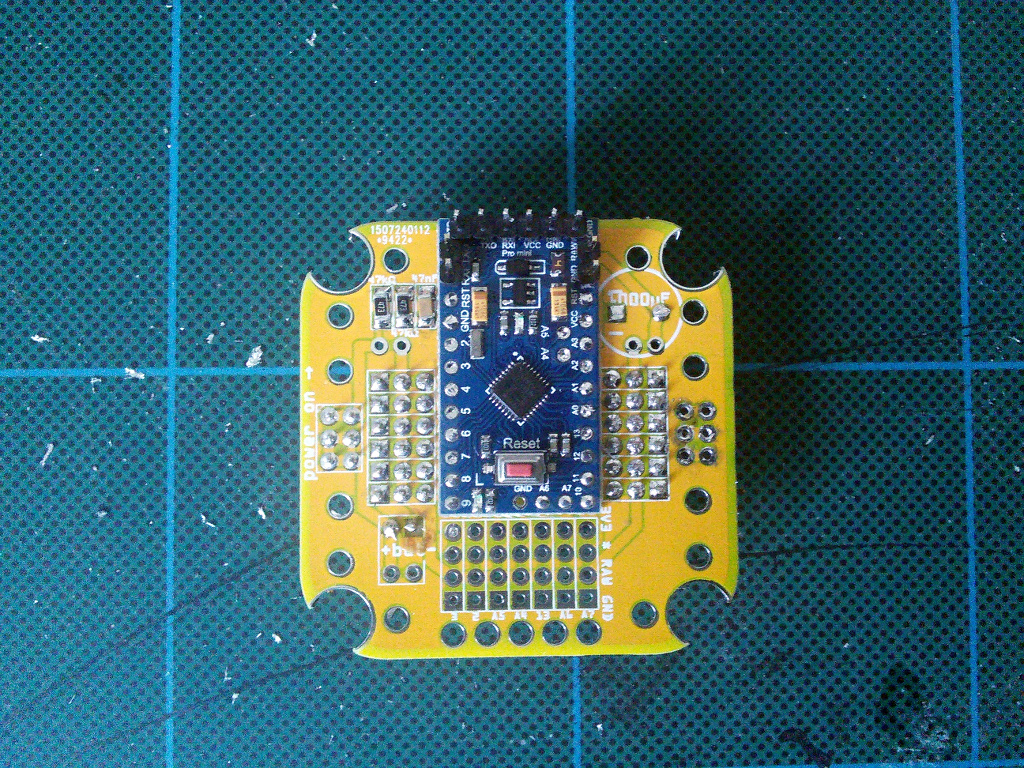
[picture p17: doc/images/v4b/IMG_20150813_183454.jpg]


The first approach is recommended when you want to experiment with a lot of
different programs and be able to easily swap the microcontrollers, each of
them running different code, or when you want to replace the default Pro Mini
with a different microcontroller.

The second solution is better when you plan on attaching an additional board
to communicate with the Pro Mini and provide higher-level control.

The Servo Headers
=================

Start by soldering the pin headers for connecting the servomechanisms. You will
need six pin male pin headers, with six pins each. You can obtain four of them
headers by breaking in half the pin headers that were added to your Pro Mini
module, however, you will need at least two more.

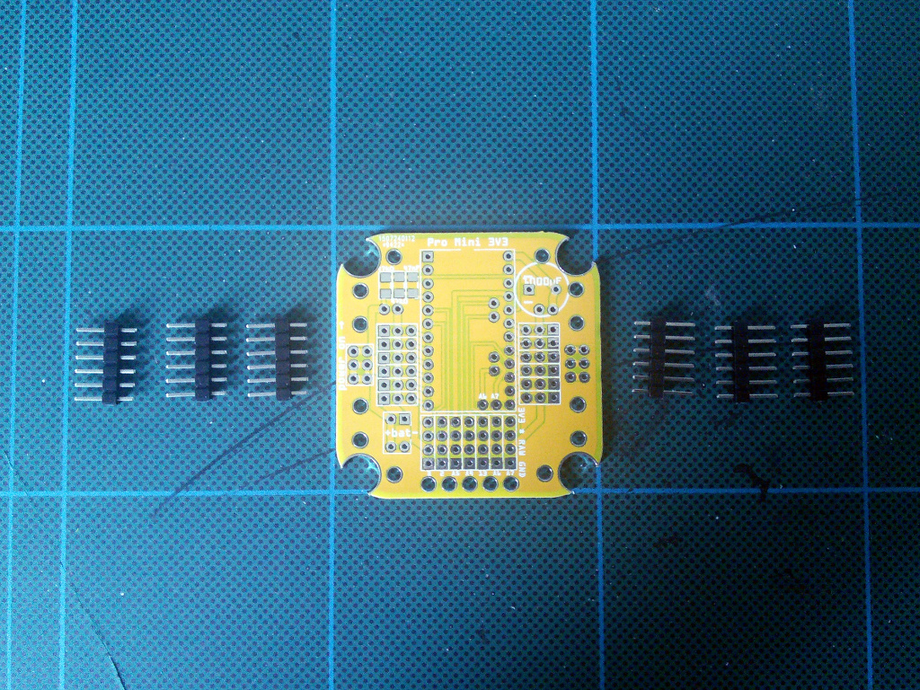
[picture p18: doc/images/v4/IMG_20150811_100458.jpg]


Insert the first pin header in its place, and solder the first pin, by touching
the soldering iron to the pin and the pad, heating it for a moment, and then
touching the pad with the solder.

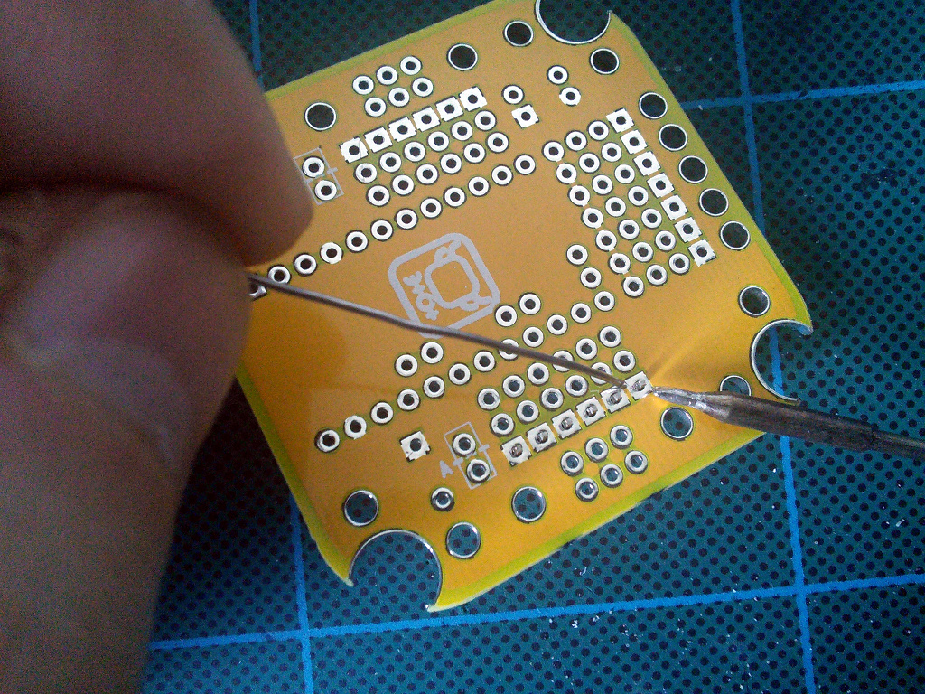
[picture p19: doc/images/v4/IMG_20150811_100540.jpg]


After soldering the first pin, always rotate the board and check whether the
pin header is straight. If it's not, melt the solder and align the header
properly. This will be impossible to fix after you solder the rest of the pins,
so remember to always do it.

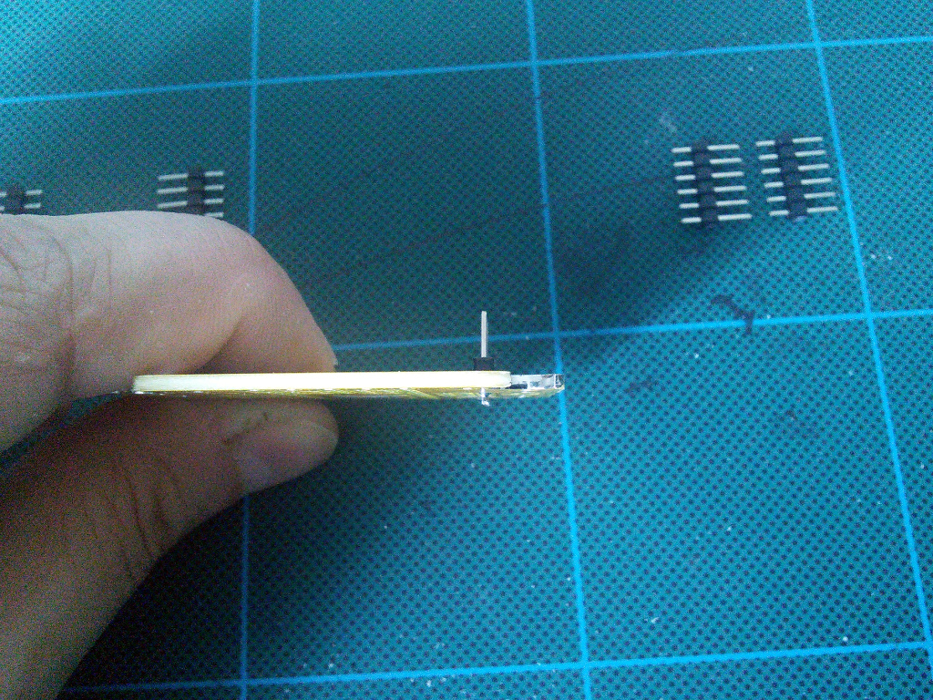
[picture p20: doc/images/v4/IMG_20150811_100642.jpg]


Repeat that for all six of the headers.

Battery Header and Optional Jumper Headers
==========================================

Prepare two-pin headers for the battery connector and, optionally, jumpers.
There are two optional jumpers you can have on the board, marked A and B.

The A jumper lets you disconnect the microcontroller's power from the rest of
the robot. This is useful if you want to power it separately, or don't want
the servos to use power when you are programming the microcontroller from the
computer.

The B jumper lets you plug between the power switch with the battery monitoring
circuit, and the rest of the robot. Use it if you want to add an additional
voltage regulator or boost converter.

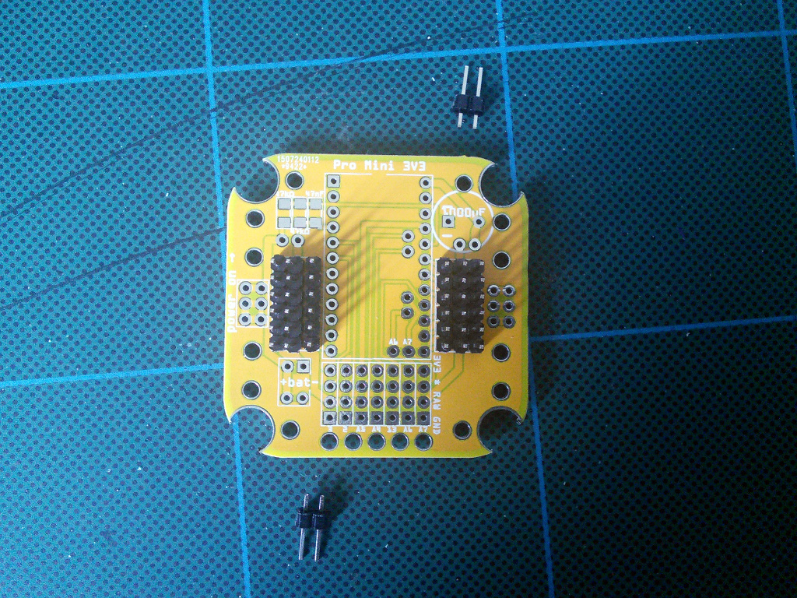
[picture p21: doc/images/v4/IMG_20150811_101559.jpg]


If you want to use the jumpers, remember that you have to cut the traces that
connect them on the underside of the board. The cutting place is marked with
a dashed line:

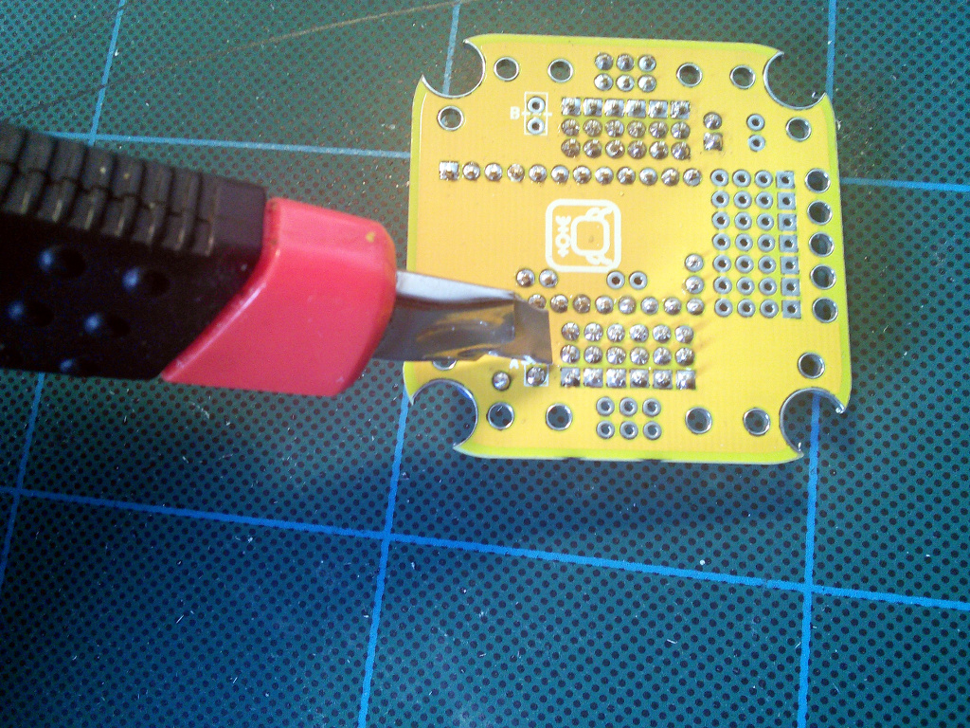
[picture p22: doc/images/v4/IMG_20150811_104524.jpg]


Note that it may be more convenient to use an angled header for the battery
connector.

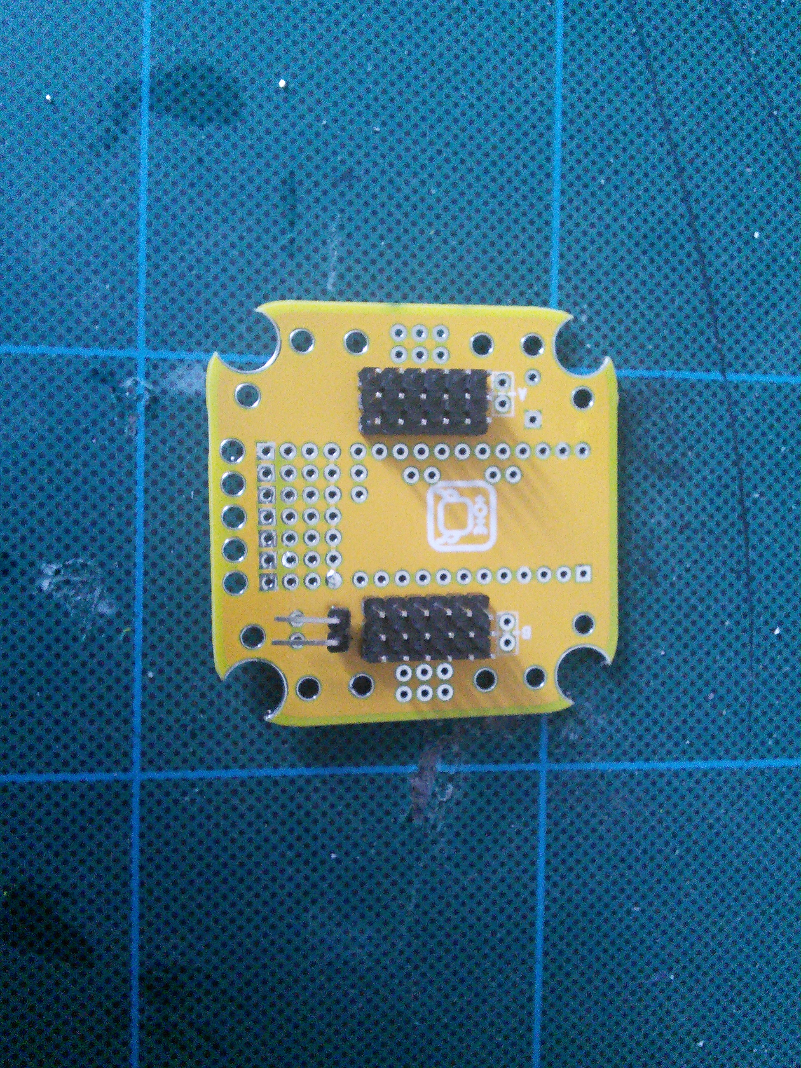
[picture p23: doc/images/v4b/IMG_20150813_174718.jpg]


Optional Microcontroller Socket
===============================

If you want the microcontroller board to be pluggable, you will need additional
female headers for making the socket. You will need two 12-pin headers, and two
2-pin ones. You can cut longer headers to make them. Start with the long ones:

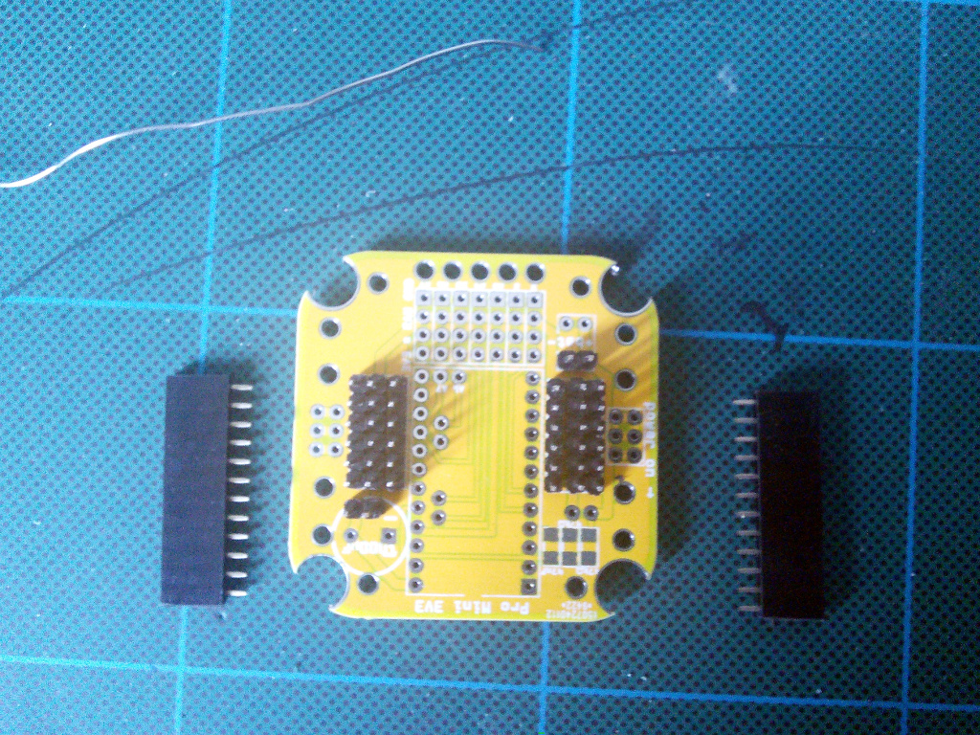
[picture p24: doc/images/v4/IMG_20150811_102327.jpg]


And then add the two short ones:

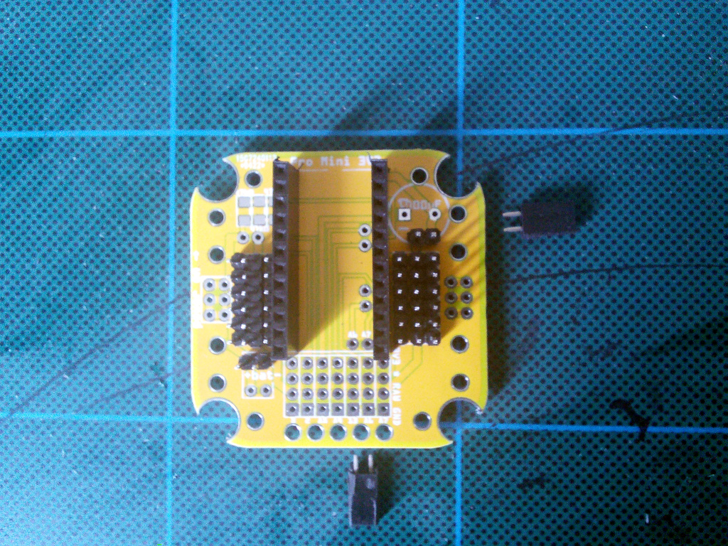
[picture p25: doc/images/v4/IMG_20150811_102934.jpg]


Note, that there are two versions of Pro Mini, differing in where the pins A6
and A7 are located. This board works with both of them, just pick the right
place for one of the short headers.

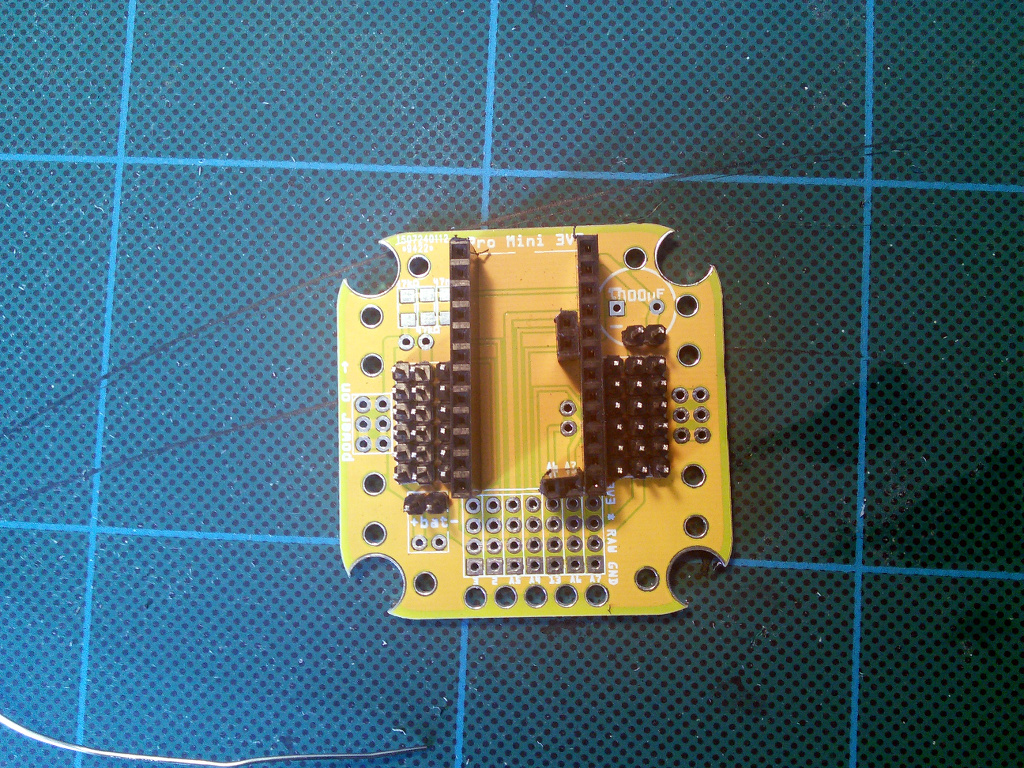
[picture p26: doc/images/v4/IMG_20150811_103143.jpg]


Alternative, Solder the Microcontroller Directly
================================================

Start by soldering the FTDI headers to the Pro Mini board. Shift the plastic
part so that the pins don't protrude on the back of the module -- we want it
to be almost flat.

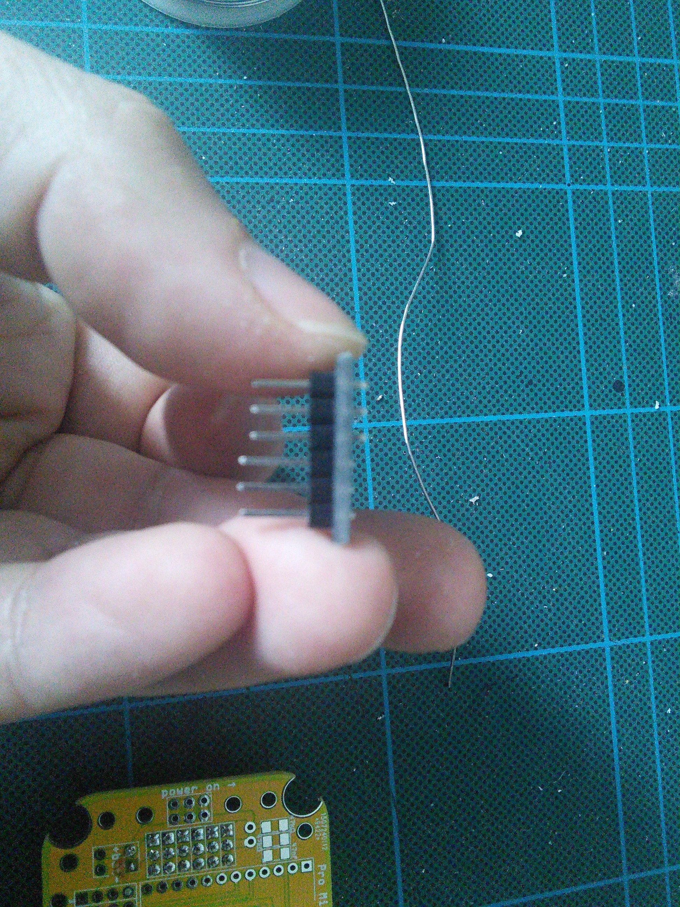
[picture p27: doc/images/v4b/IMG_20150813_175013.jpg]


Add additional pins for the battery and serial connections for your extension
boards:

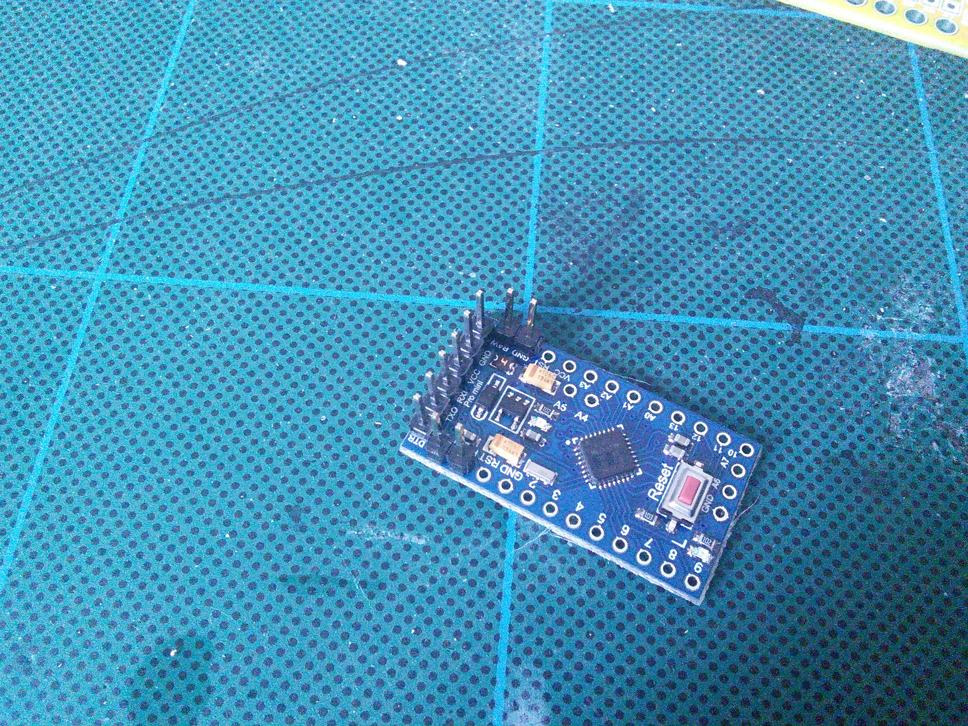
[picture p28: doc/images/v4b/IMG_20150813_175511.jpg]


Now fill the holes in both the board and the module with solder:

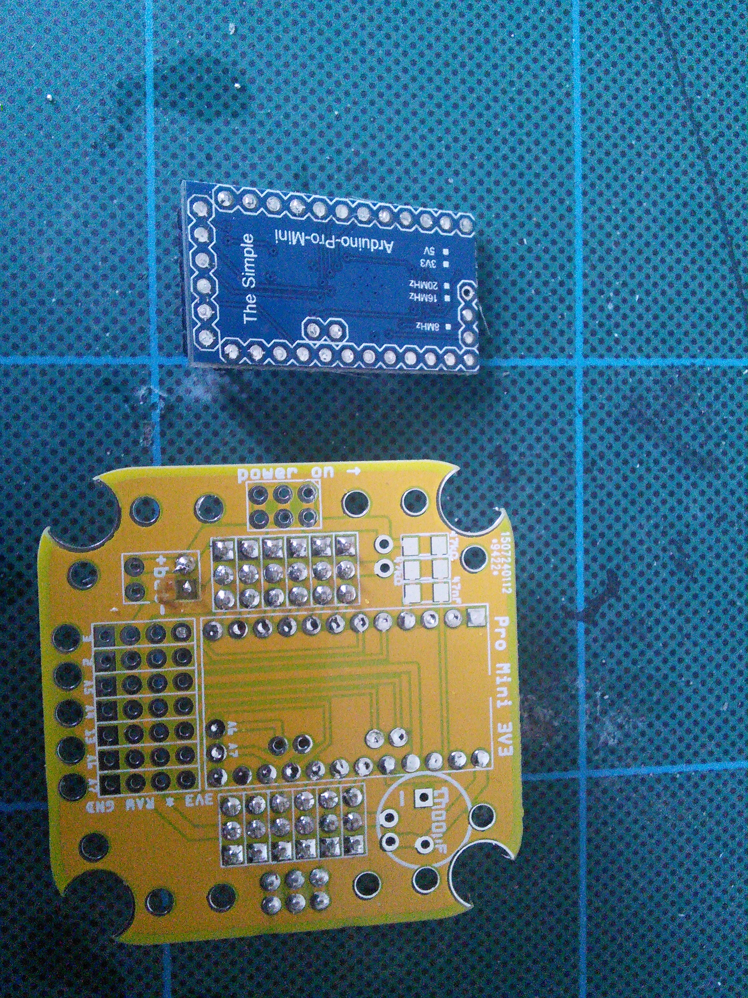
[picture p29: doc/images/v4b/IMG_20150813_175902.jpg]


Place the module on top of the board, carefully align it, and melt the solder
in each of the holes with your soldering iron, so that they fuse. Make sure you
get proper connections here. It's recommended to check each connection with a
multimeter, and retry if it's bad.

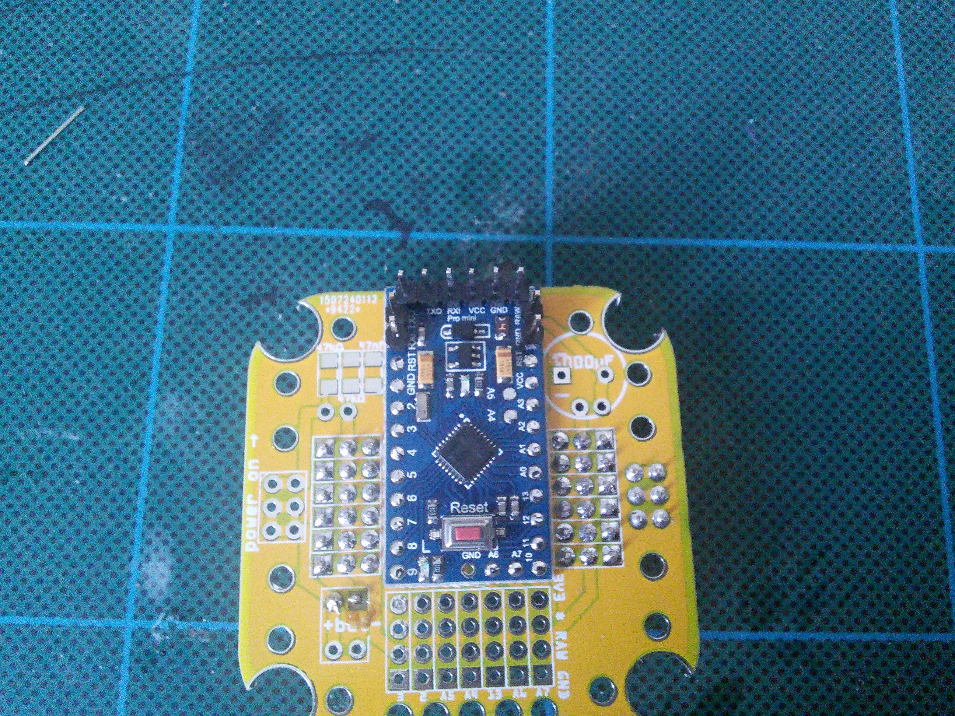
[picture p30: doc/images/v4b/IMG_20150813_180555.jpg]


Optional Battery Monitoring Circuit
===================================

Since the battery has higher voltage than the 3.3V our Pro Mini uses, we need
to lower it to be able to measure it, using a voltage divider. This circuit
consists of two 47kΩ resistors and one 47nF capacitor in the upper left corner
of the board:

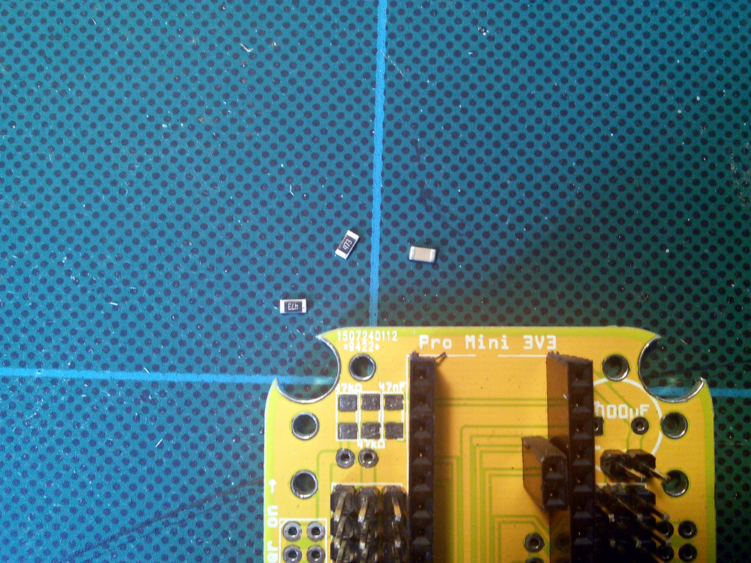
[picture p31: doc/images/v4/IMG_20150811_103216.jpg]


Place each of the parts in the right spot, and solder one end of it:

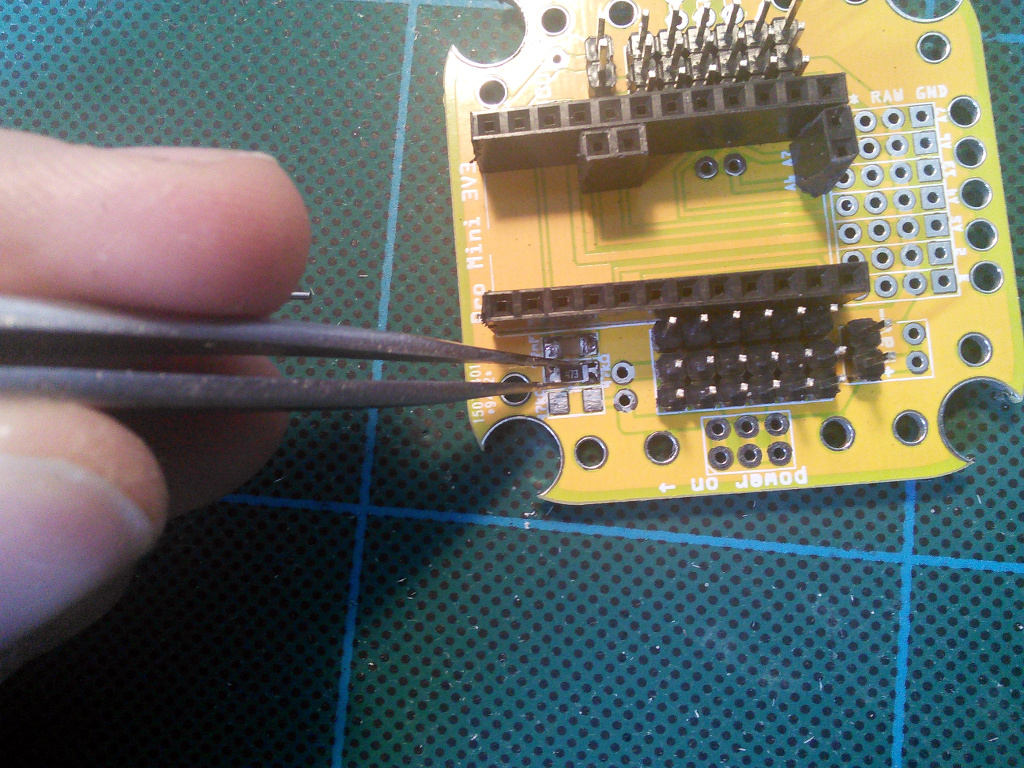
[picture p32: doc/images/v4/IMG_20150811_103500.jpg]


When it's in the right position, solder the other end:

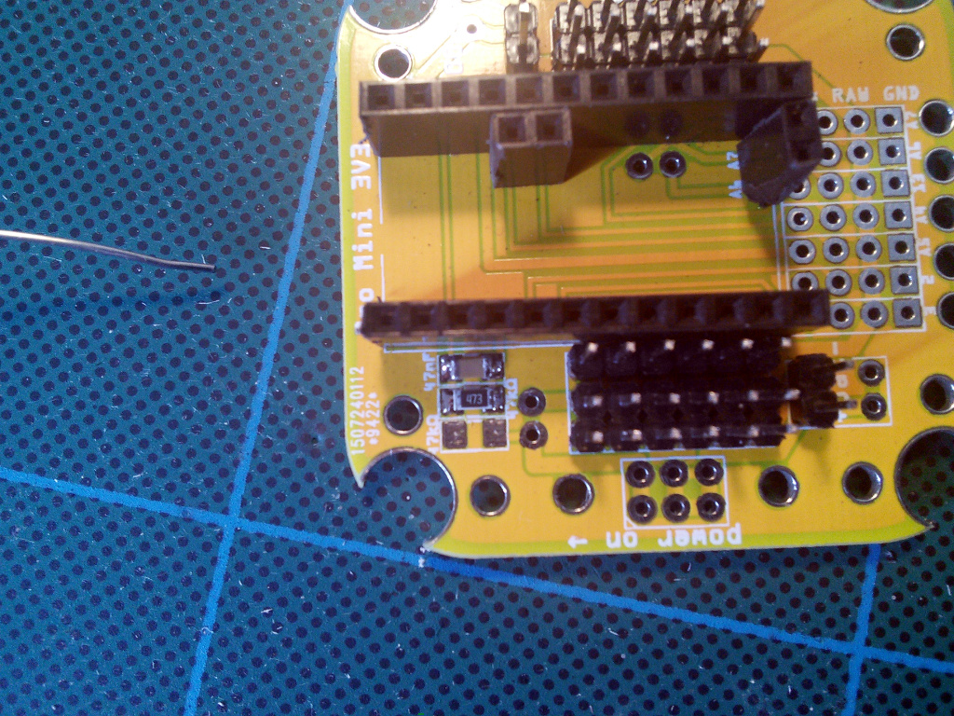
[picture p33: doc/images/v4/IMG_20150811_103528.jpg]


Repeat that for each of the parts:

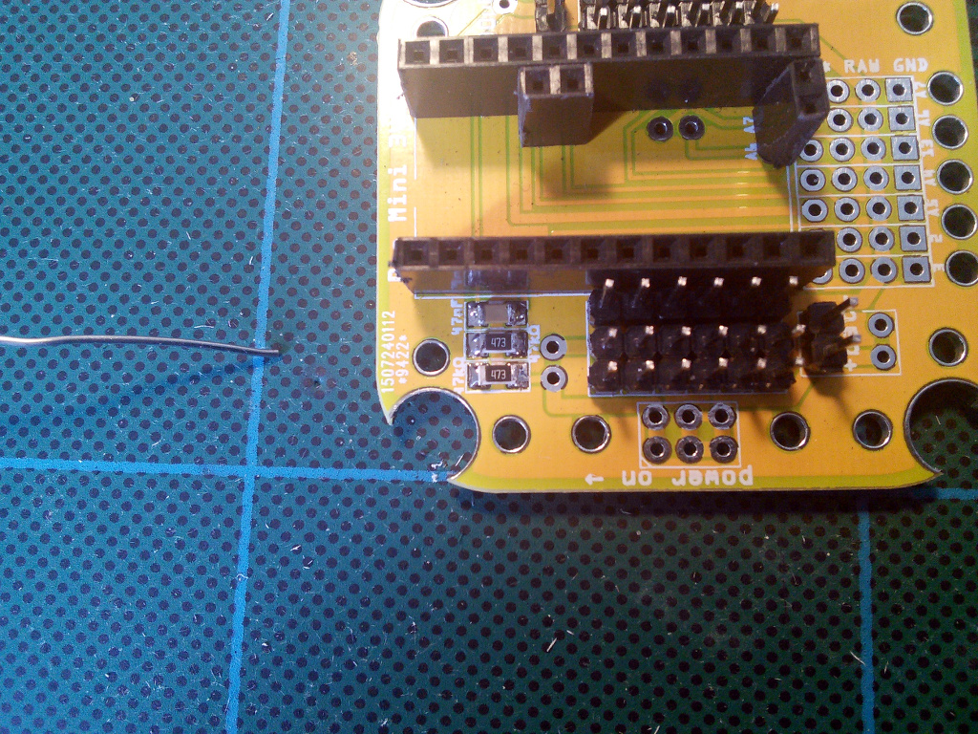
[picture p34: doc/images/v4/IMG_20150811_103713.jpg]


Optional Anti-brownout Capacitor
================================

This capacitor makes sure that the microcontroller has enough current even when
the servos momentarily use all the battery can give. It has its place in the
upper right corner of the board. Pay attention to the markings on the capacitor
and the board, to make sure the negative lead goes into the right hole --
electrolytic capacitors are polarized and connecting them wrong may make them
explode.

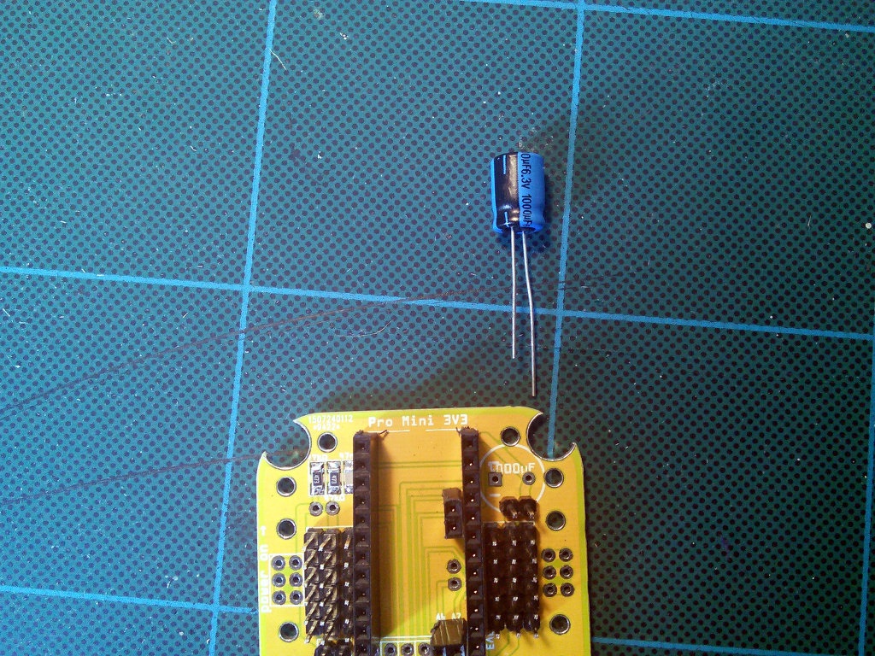
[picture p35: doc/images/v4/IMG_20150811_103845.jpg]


The negative lead is usually marked with a dark strip.

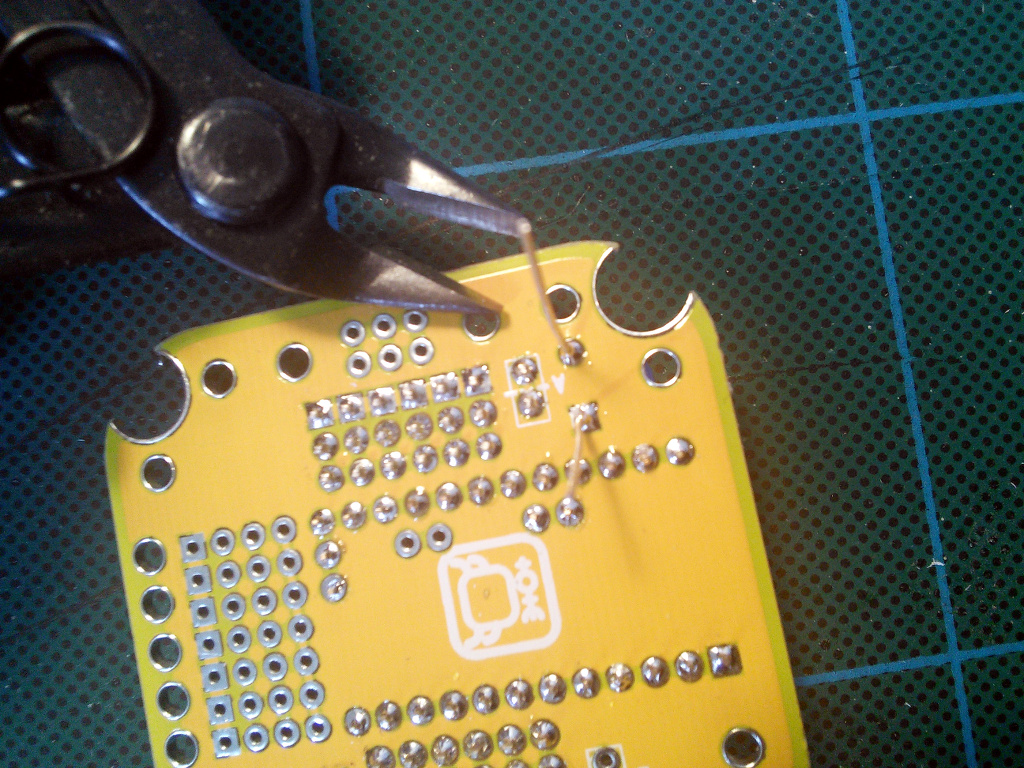
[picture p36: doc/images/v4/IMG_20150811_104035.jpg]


Cut off the excess leads from the other side.

Power Switch
============

The power switch goes on the left edge of the board. Pay attention, as there is
a similar set of holes on the other side, but they should be left unpopulated.
You can use them later, when extending your robot.

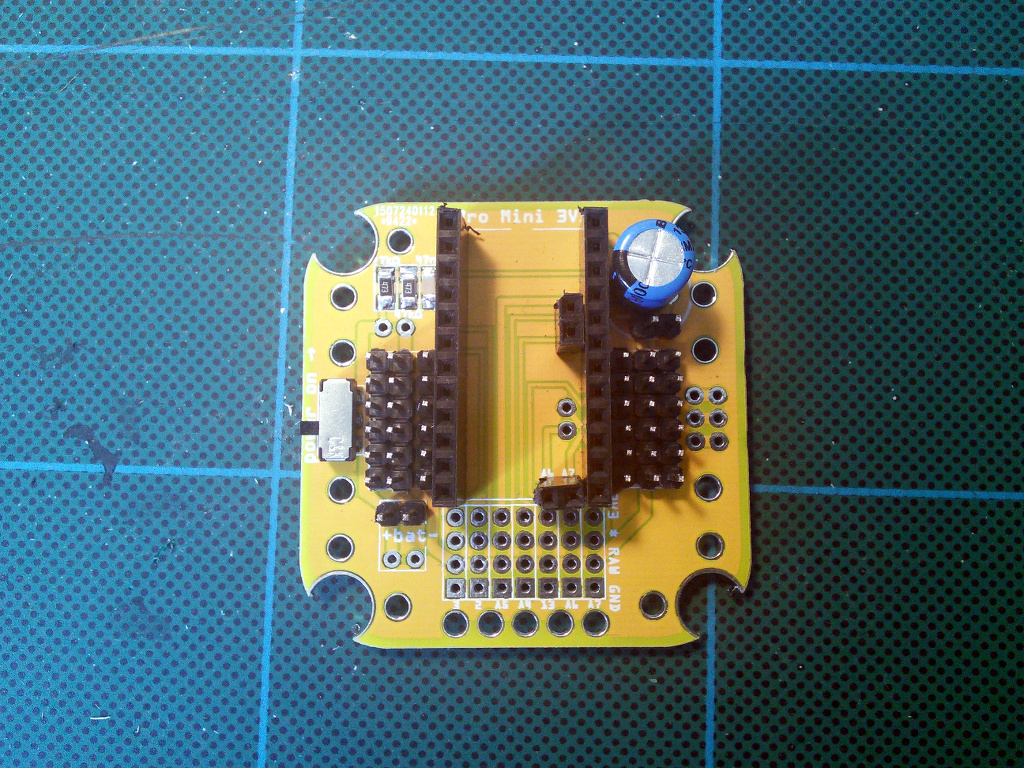
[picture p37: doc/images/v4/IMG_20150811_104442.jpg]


Optional IR Receiver
====================

If you want to control your robot using a TV remote, you will need to add an
infra-red receiver. Practically any 38kHz module will do, I have tested
TSOP4838, LF0038Q and VS1838B.

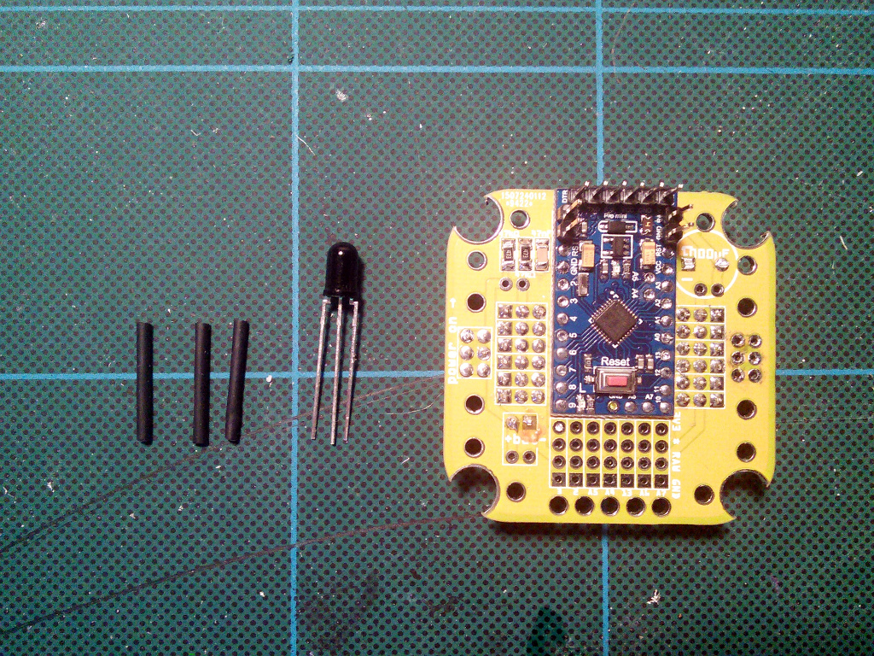
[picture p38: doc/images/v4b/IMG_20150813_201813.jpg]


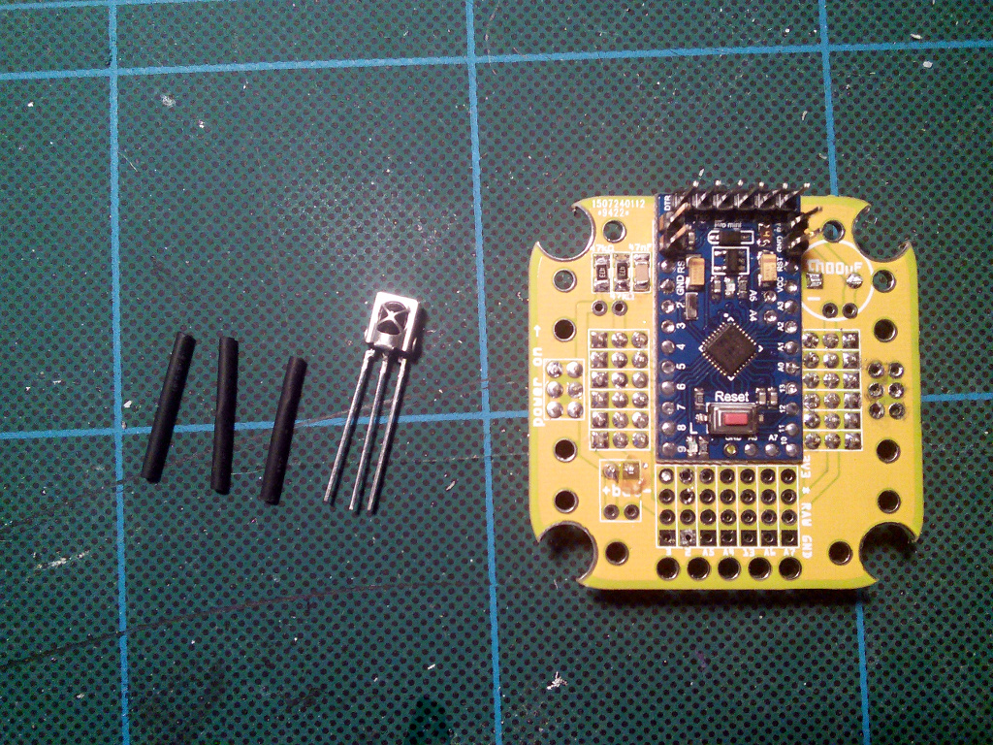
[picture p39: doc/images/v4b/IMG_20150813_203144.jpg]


The only thing you have to be careful about is to connect the right leads to
the right holes: GND to ground, VCC to 3V3, and OUT to pin 2. To do it, you
will have to cover the leads with isolation and bend them, as they will most
likely be in the wrong order. Check the datasheet of your part for details.

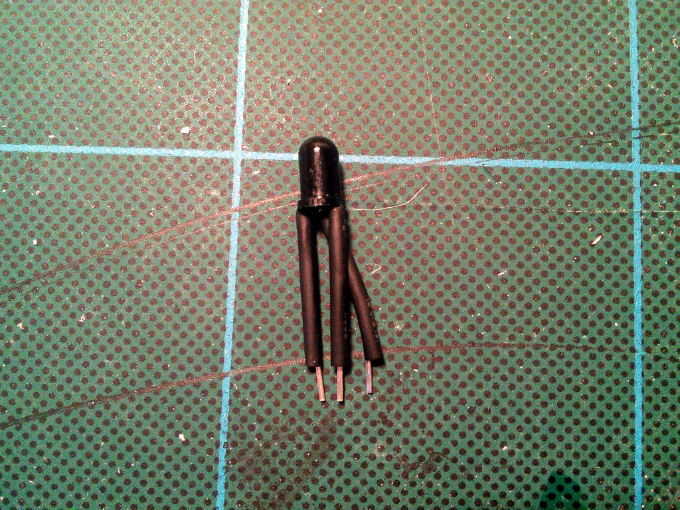
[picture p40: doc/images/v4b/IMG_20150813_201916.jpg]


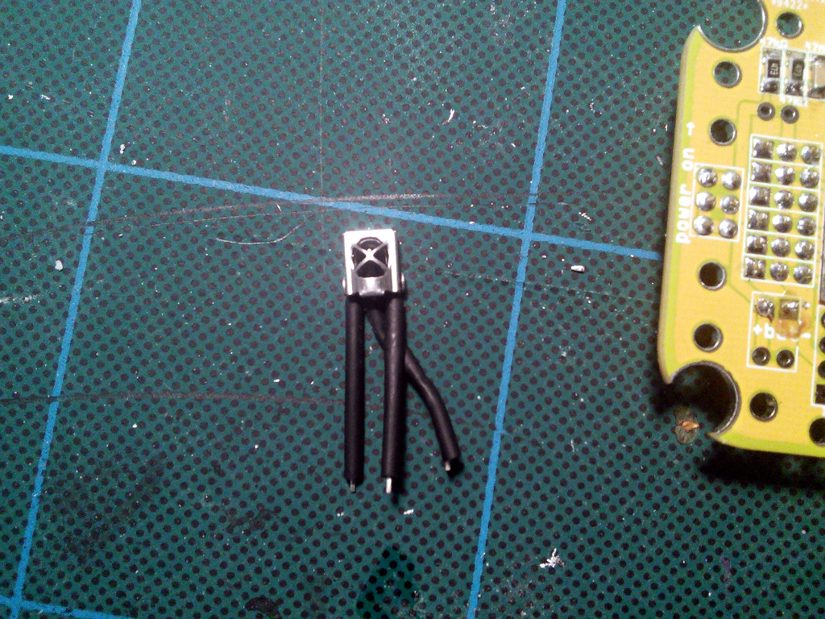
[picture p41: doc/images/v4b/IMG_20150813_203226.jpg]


Unlike previous boards, there is no special place to put the sensor. We want
it to be connected to pin 2, which is broken out with all other free pins:

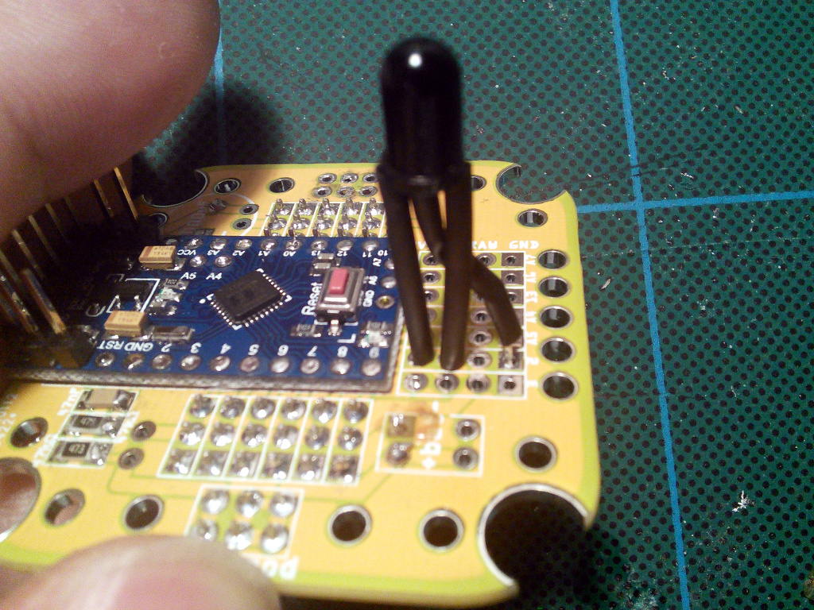
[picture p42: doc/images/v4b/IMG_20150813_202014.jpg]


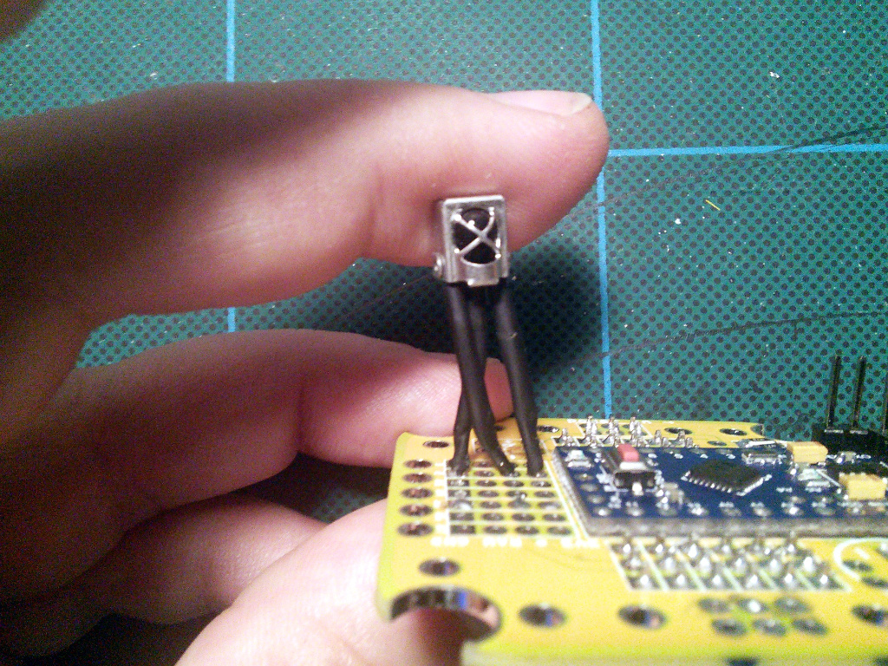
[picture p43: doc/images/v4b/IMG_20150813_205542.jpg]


Then just solder it in place:

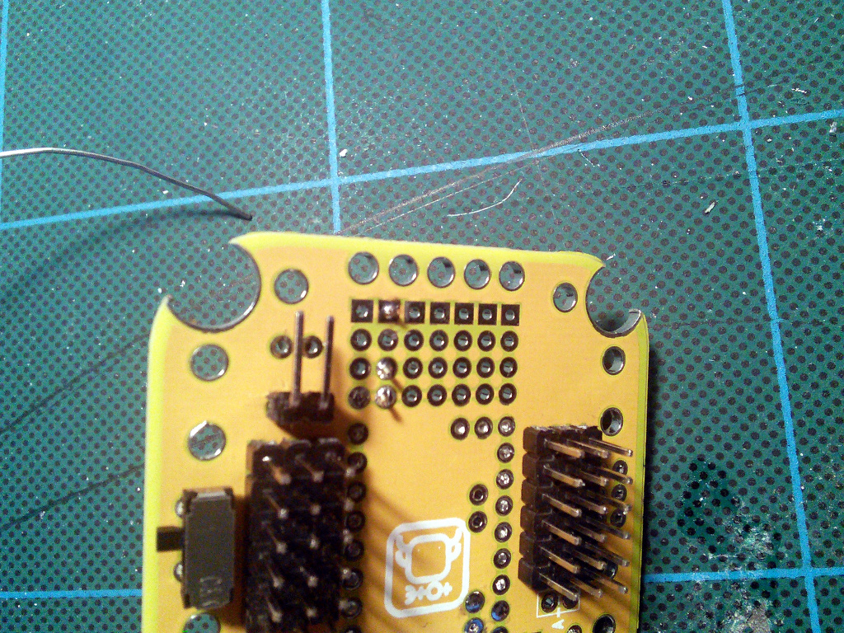
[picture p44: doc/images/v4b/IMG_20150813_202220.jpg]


Optional Piezo Buzzer
=====================

If you want your robot to be able to make sounds, you can add a piezoelectric
speaker on pin 13 -- the same as the build-in LED. Any kind will work fine.
Cut the leads to a convenient length:

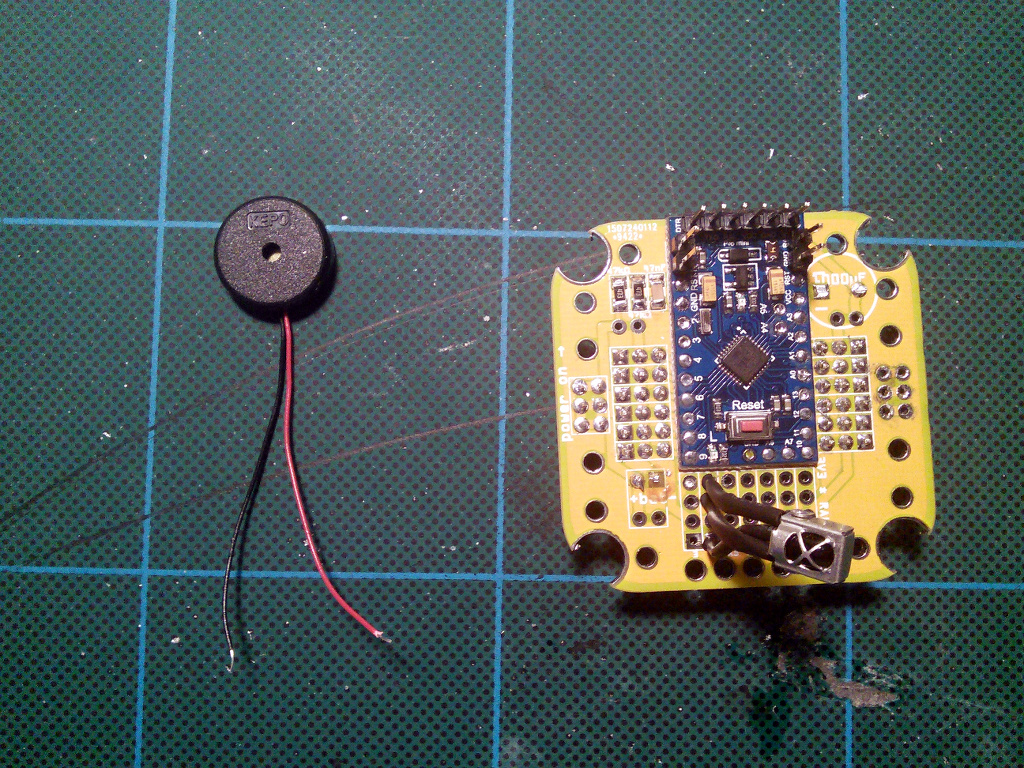
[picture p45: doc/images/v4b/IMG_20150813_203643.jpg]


Then solder the speaker to the ground and pin 13:

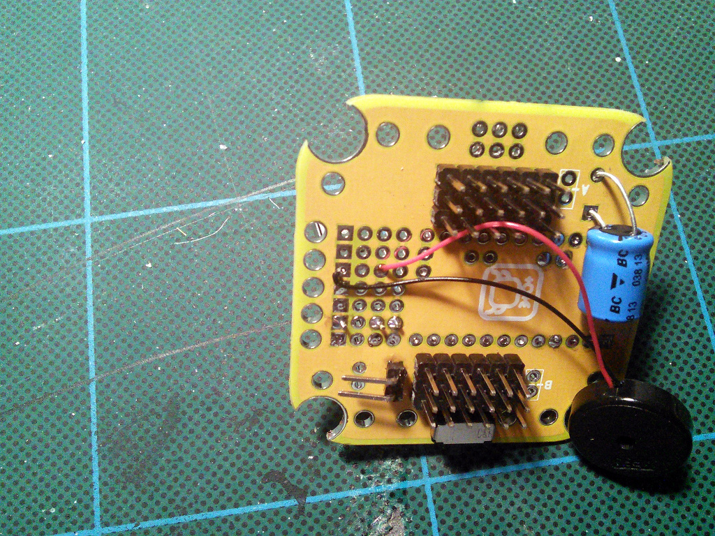
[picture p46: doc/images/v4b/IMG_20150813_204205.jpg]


Glue the speaker under the board.

Servo Horns
===========

Insert the single-armed horns that you got with the servos into the large holes
in the corners of the board. Depending on the exact model and manufacturer of
the servo, the horns may be too big to fit -- then you have to use a file to
either make the holes a little larger, or the horns a little smaller.

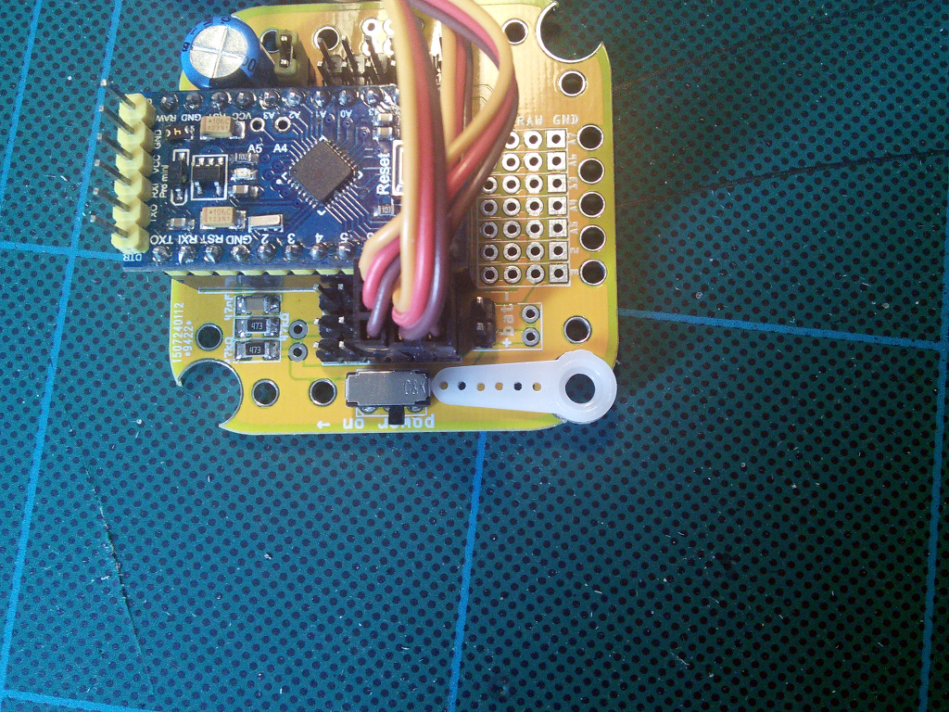
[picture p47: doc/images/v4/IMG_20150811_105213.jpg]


Attach the horns with two screws each:

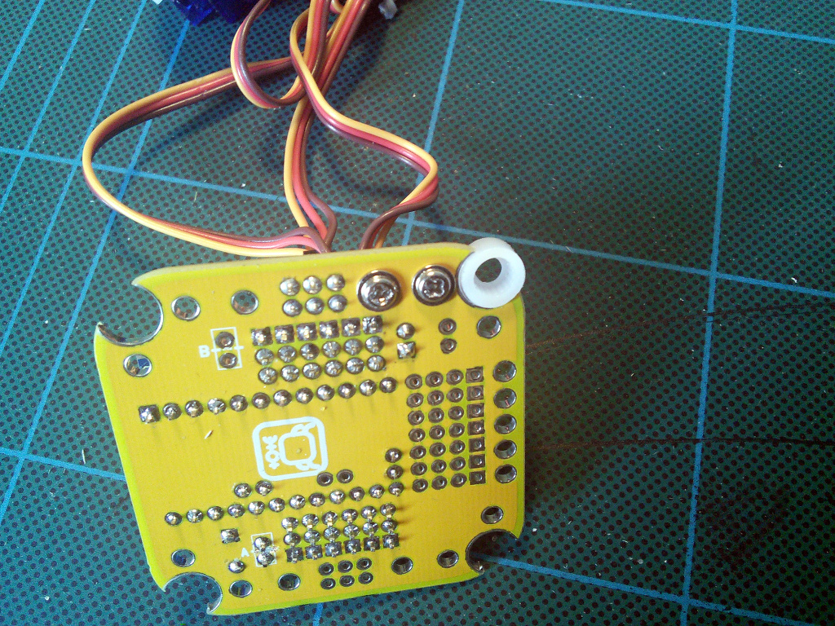
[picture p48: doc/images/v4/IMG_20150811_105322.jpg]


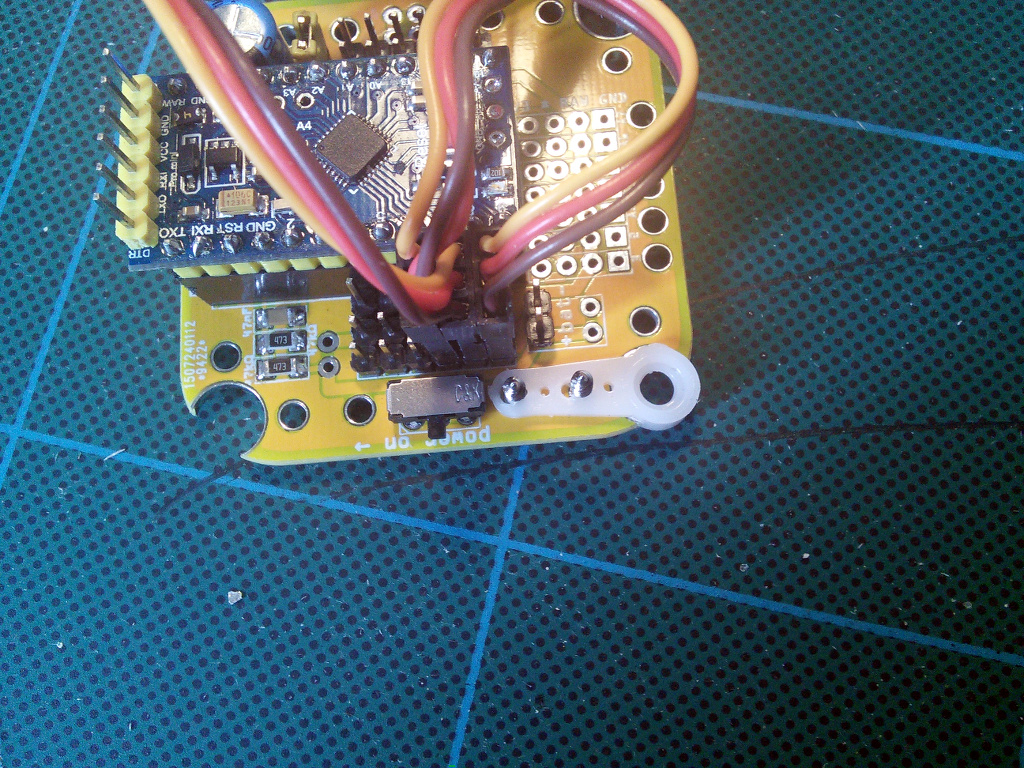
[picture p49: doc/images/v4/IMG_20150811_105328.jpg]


And then you can attach the leg servo:

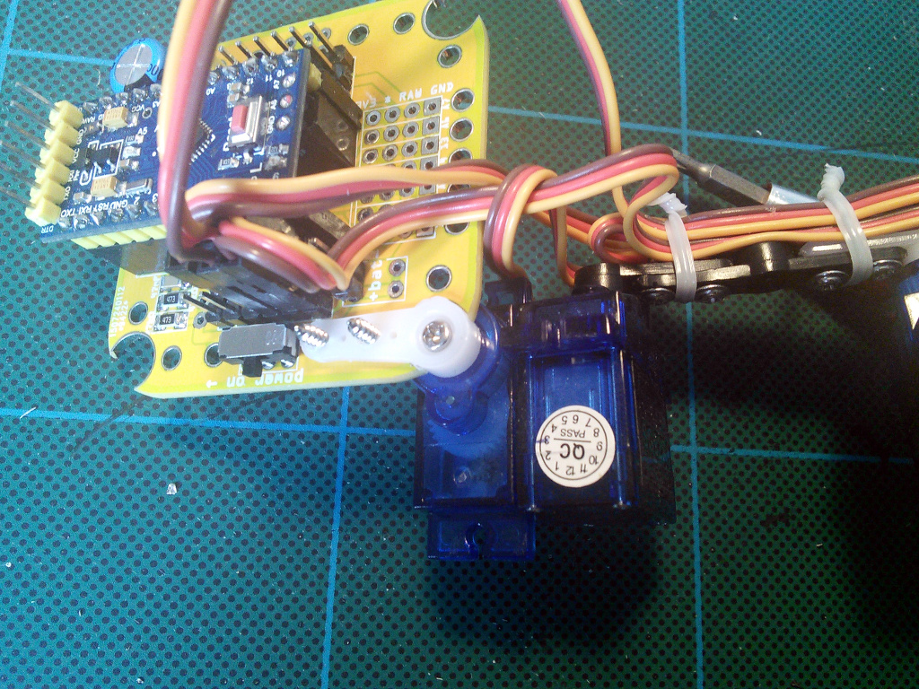
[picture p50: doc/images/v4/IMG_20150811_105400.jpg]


Make sure it can rotate freely, without heating the heads of the screws. Use
a file if there is a problem.

Note that when attaching the legs to the body, you will need to adjust the
angles servo horns -- all previous versions of the board had the horns
attached diagonally, but this version has them in parallel to the board. That
means that you have to remove the screw, remove the horn, rotate the whole leg
by 45°, put it back into the horn, and replace the screw. At the neutral position the leg should be sticking out at 45° from the body, shown here:

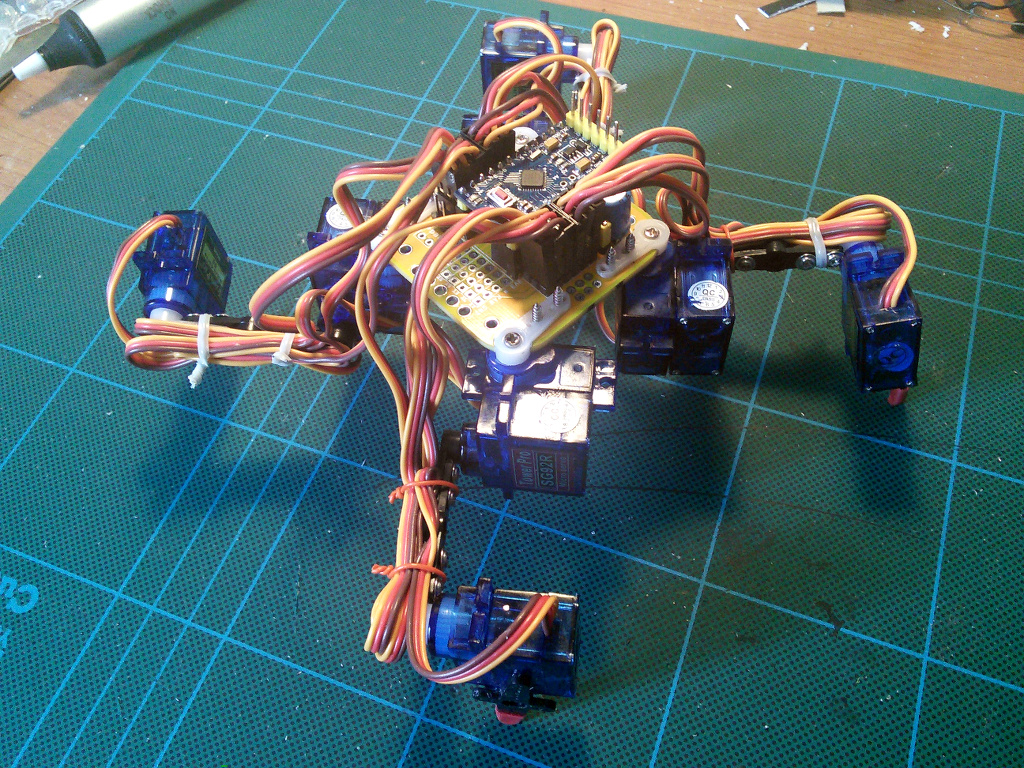
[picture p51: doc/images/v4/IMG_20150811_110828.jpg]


Legs
====

Now it's time to assemble the robot's legs. You will need 12 small servos, with all the screws and the horns that come with them.

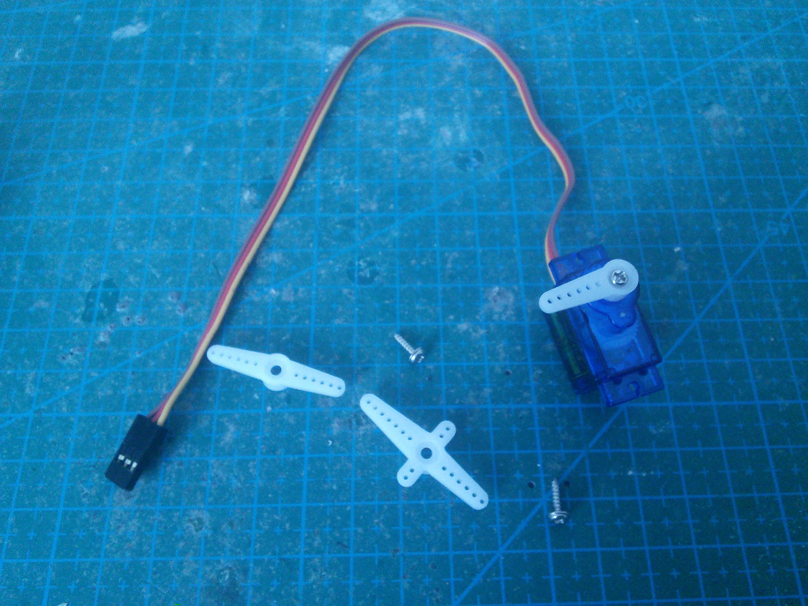
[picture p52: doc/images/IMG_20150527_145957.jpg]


Set all the servos to the zero position (in the middle of their movement
range). Then attach the single-arm horn at 90°. You will need six servos with
the horn in one direction, and six servos with the opposite. Fasten the horns
with the smallest screws (always make sure you un-power the servo before you do
that).

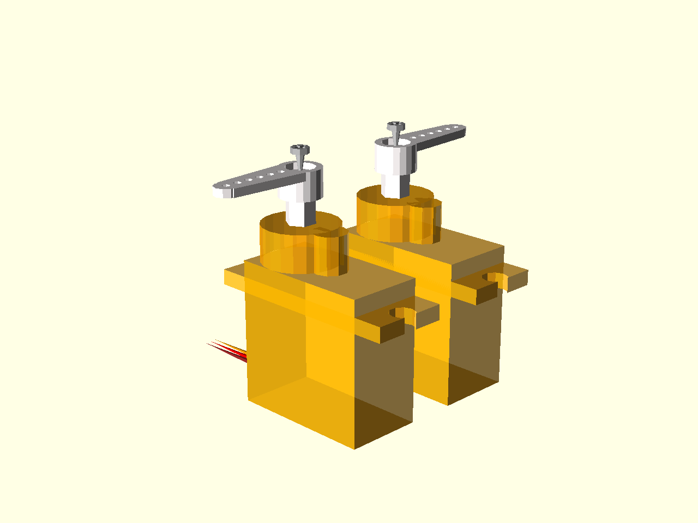
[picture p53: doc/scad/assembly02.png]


Put the legs together.

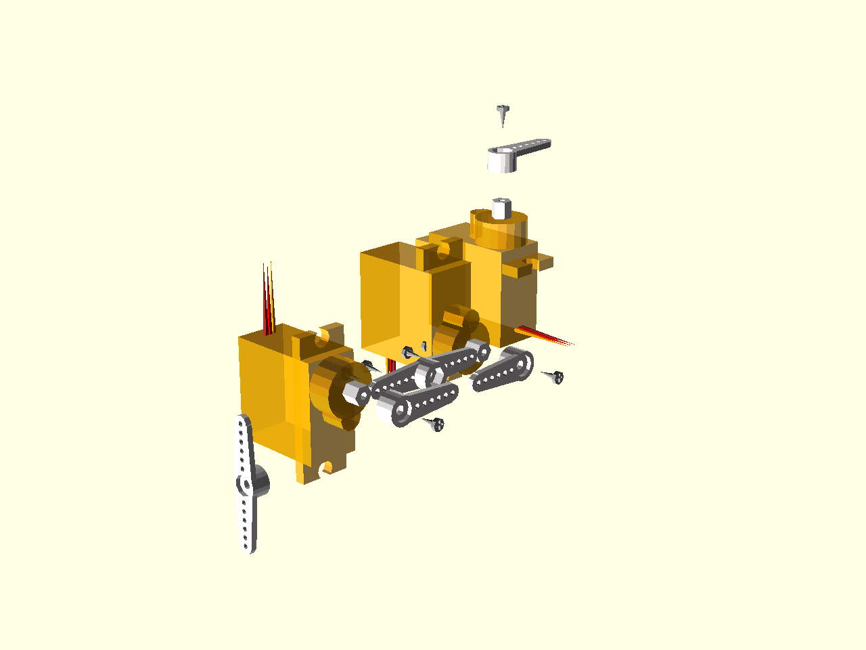
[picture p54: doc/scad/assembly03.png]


Screw the bigger screws into the double servo horn . You will need to use some
force, because the holes in the horns are much smaller. Fortunately the plastic
is quite soft.

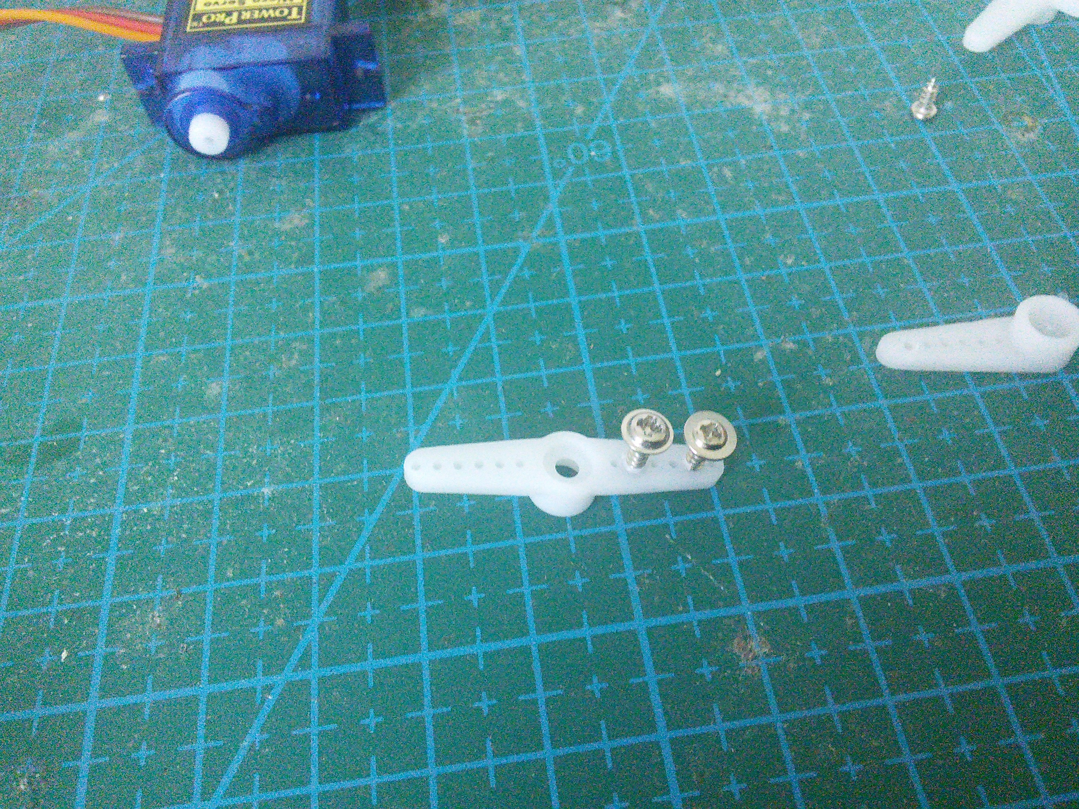
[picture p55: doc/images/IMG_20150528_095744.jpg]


Now attach the single horn to that. Repeat for the other side.



If you want, you can cut off the parts of the screws that are sticking out (or
use some smaller screws to begin with).

Remove the stickers from the servos. We will need to apply some glue there, and
the stickers are in the way.



Attach the horns to two servos. You will need two right legs, and two left
ones, that are their mirror images.



Glue the leg to the servo on the body. I recommend an epoxy glue, but as you
can see, you can even use a two-sided tape. Make sure the alignment is straight.



Finally, glue a double horn at the end of the leg, as the leg tip. I like to
use the slightly longer horn here (the cross-shaped one), as it is lightly
longer. Note that two-sided tape doesn't work very well here, as the area is
too small for it to stick properly. Use glue.



You can put a piece of rubber (a small rubber hose works best) at the tip of
the leg, to give the robot better traction.

Connect all the servos plugs into their respective sockets. The outermost
socket for every leg is the hip, then knee, then ankle. Make sure the yellow
wire is on the inside, and the brown one on the outside.



If you want, you can tie the cables together to make the robot look better and
to avoid tangling. Make sure you leave enough loose cables for the legs to move
freely.



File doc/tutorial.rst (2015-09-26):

Step-by-step Tutorial
*********************

This tutorial should take you through all the steps you need to design a
walking robot like the Tote. It's for people who are not satisfied with just
blindly following a ready blueprint, but would rather want to be able to design
their own robots. This takes considerably more time, than just assembling a
robot, but it can be done one small step at a time.

Soldering the Pin Headers
=========================

In order to be able to connect your Pro Mini to your computer, you first need
to solder the pin header for the serial communication. Your board should have
come with with three pin headers: one 6 pins long, and two 12 pins long. You
will need the shorter, 6 pin long one. The pins in it may be straight, like in
the illustrations, or they may be angled -- it doesn't matter for our purposes.

Insert the pin header into the holes at one of the short ends of the board, as
the illustration below shows:



Now flip the board to the other side, place it on a table, and carefully solder
each of the pins to their holes. To do that, first touch the hole with the end
of your solder wire, and then briefly touch it with a hot soldering iron, as shown below:



The solder should melt and flow into the hole, filling it and securing the pin
in place. Make sure you don't connect the neighbouring pins with each other
while doing this. Each of them should have a separate electric connection only
to their own hole.

Connecting the Pro Mini to the Computer
=======================================

Unlike most other Arduino boards, the Pro Mini cannot be directly connected to
your computer's USB port. Instead, you will need to use a small device called
USB2TTL adapter, which basically contains all the electronics required to
support a USB connection that the Pro Mini is missing. This makes the Pro Mini
much cheaper than the other boards, and you can re-use the adapter for other
projects. You will also need a cable to connect the USB2TTL with your board.
It's simply 5 wires, with small sockets on both sides, which slide onto the
pins that you just soldered, and onto the pins of the adapter. You have to pay
very close attention to which pins you are connecting, though. Look at the
symbols on both boards, and connect the pins like this:

 * The DTR pin on the Pro Mini connects to the DTR pin on the adapter.
 * The TXD (or simply TX) pin connects to the RXD (or RX) pin.
 * The RXD (or RX) pin connects to the TXD (or TX) pin.
 * The VCC pin connects to the 5V (or VCC) pin.
 * The GND pin connects to the GDN pin.

If your adapter lacks the DTR pin, don't worry, you can skip it, but then you
will have to manually restart your board each time you are uploading code into
it.

Once you made all the connections, insert the USB2TTL into your computer's USB
port. If everything went right, and your Pro Mini is brand new, you should see
one LED on it light up (it's the power indicator), and another LED blink about
once a second. This is the default "demo" program that is uploaded to all new
Arduino boards, and it shows that your board is working.

Uploading First Arduino Program
===============================

In order to actually write and upload programs onto your board, you will need
the Arduino IDE software. You can download it from the Arduino website for your
platform of choice. Refer to the information on that website for help with
installing and configuring it.

Once you have that working, you can select the "blink" example from the
examples menu, select the right board type (Pro Mini 3.3V), connect your board
and hit the "upload" button. With a little luck you will have your own "blink"
program uploaded. To verify that it works, you can change the delay between
blinks, and upload it again.

Blinking a LED from the Computer
================================

Attaching a Buzzer and Making Sounds
====================================

Attaching an RC Servo
=====================

Controlling the Servo and Buzzer from the Computer
==================================================

Attaching an Infra-Red Sensor
=============================

Blinking a LED, Making Sounds and Moving Servos with a TV Remote
================================================================

Making a Pan-and-tilt Gimbal
============================

Attaching a Battery
===================

Assembling the Printed Circuit Board
====================================

Monitoring Battery Voltage
==========================

Quadruped with Two Degrees of Freedom per Leg
=============================================

Leg Inverse Kinematics
======================

Unbalanced Crawling
===================

Crawling Sideways
=================

Rotating in Place
=================

Turning While Crawling
======================

Changing Body Height
====================

Shifting the Body
=================

Balanced Crawling
=================

Trotting
========

Attaching a Proximity Sensor
============================

Following an Object
===================

Avoiding Obstacles
==================

Attaching a Bluetooth/WiFi Module
=================================

Telemetry
=========

Attaching an Accelerometer
==========================

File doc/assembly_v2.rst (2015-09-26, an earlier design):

Assembly Instructions for PCB Version 2
***************************************

Electronics
===========



Gather all the electronic components that you will need. At the minimum, you
will need the printed circuit board, the pin headers and the Pro Mini module.
Optionally a 1000µF capacitor, power switch, IR receiver and the battery
monitoring circuit consisting of two 47kΩ resistors and a 47nF capacitor, can
be added. They are all recommended, so we will assume there are there.

There are two ways of assembling the electronic components for Tote. The first
one is compact, like this:



The second one takes up more space, but lets you remove and replace the Arduino
module. You will need additional female and male pin headers for that:



Throughout the rest of this guide, we will assume the first, compact, version.

All the electronic components need to be soldered onto the printed circuit
board in the right places, as follows:



We will start with the pin headers. First, you have to cut seven pieces, each
of them exactly 6 pins long.



You will also need one header that is 2 pin long, for the battery.



Solder six headers for the servo sockets. Make sure they are straight when you
are soldering the first pin -- it's almost impossible to straighten them later.



And also solder the battery connector in place. You should have one 6-pin
header left. We will need it later.



Now it's time to solder the battery monitoring circuit. First arrange the
elements on the board.



Then carefully solder each one in place.



Finally, solder the remaining header onto the Pro Mini module, so that you can
program it.



Now place the Pro Mini on the PCB, and put a drop of solder into every hole.

.. warning::

    This is not the best way to get a proper electric connection. After some
    experimenting, I recommend inserting a piece of wire into the hole before
    soldering, and then cutting it once it's soldered in place. Debugging bad
    connection is really not fun.



To make sure there is a good electric connection, repeat that from the other
side.



Now add the power switch. If you have one with 6 pins, just ignore (or cut off) the remaining 3 pins.



Since we are not using a voltage regulator, we need to short the pads that
would be used for it. Just solder a small piece of wire in there. You can later
remove it if you want to add a voltage regulator.



The 1000µF capacitor has to be soldered with the right polarity. Make sure that
the shorter leg (the one marked on the capacitor with a white strip) goes to
the hole with a small minus next to it.



Don't solder the capacitor tightly fitting the board -- best leave some wires
from the legs (don't forget to isolate them), so that you can bend it out of
the way when needed. Remember, that you will need to screw in the legs in
there.



Prepare the IR sensor for soldering. Make sure you check the datasheet for your
particular sensor, and bend the legs so that the right ones go into the right
holes. In this case, I need to switch two of the legs, so I simply crossed
them.



Also leave the legs long, so that you can adjust the position of the sensor
later.



That concludes the electronics of our robot.

Programing
==========

In order to program the robot, you need to connect it to your computer. To do
that, you will need an TTL2USB module, and some Dupont cables (you can also use
an FTDI cable, or even another Arduino board). First, connect the cables to
your TTL2USB, make sure to note which color goes with which symbol.



Next, connext the other side of the cables to the Pro Mini header. Make sure
that the connections are as follows:

 * ``TX0`` - ``RXD``
 * ``RX0`` - ``TXD``
 * ``VCC`` - ``VCC`` or ``5V``
 * ``GND`` - ``GND``
 * ``DTR`` - ``DTR``

If your TTL2USB doesn't have a ``DTR`` pin, leave it disconnected. You will
need to manually press the "reset" button on the Pro Mini when programming it,
then.



Now open the ``start/start.ino`` file in the Arduino IDE, from the "Tools →
Board" menu select "Arduino Pro or Pro Mini (3.3V, 8Mhz) w/ ATmega328", connect
the TTL2USB to your computer's USB port, and click the "upload" button. If your
TTL2USB doesn't have a ``DTR`` pin, press the "reset" button on the Pro Mini as
soon as the program size appears in the black console at the bottom of the IDE.
When you see "Upload finished", you can disconnect everything and proceed.



Mechanics
=========

Now it's time to assemble the robot's legs. You will need 12 small servos, with all the screws and the horns that come with them.



Set all the servos to the zero position (in the middle of their movement
range). Then attach the single-arm horn at 90°. You will need six servos with
the horn in one direction, and six servos with the opposite. Fasten the horns
with the smallest screws (always make sure you un-power the servo before you do
that).



Put the legs together.



First, attach the four servos to the body.



Connect them to the outermost servo sockets. Make sure that the yellow wire is
inside, and the brown wire outside for all the servos.



Screw the bigger screws into the double servo horn . You will need to use some
force, because the holes in the horns are much smaller. Fortunately the plastic
is quite soft.



Now attach the single horn to that. Repeat for the other side.



If you want, you can cut off the parts of the screws that are sticking out (or
use some smaller screws to begin with).

Remove the stickers from the servos. We will need to apply some glue there, and
the stickers are in the way.



Attach the horns to two servos. You will need two right legs, and two left
ones, that are their mirror images.



Glue the leg to the servo on the body. I recommend an epoxy glue, but as you
can see, you can even use a two-sided tape. Make sure the alignment is straight.



Finally, glue a double horn at the end of the leg, as the leg tip. I like to
use the slightly longer horn here (the cross-shaped one), as it is lightly
longer. Note that two-sided tape doesn't work very well here, as the area is
too small for it to stick properly. Use glue.



You can put a piece of rubber (a small rubber hose works best) at the tip of
the leg, to give the robot better traction.

Make sure to attach the right legs in the right orientation, as on the image.



Connect all the servos plugs into their respective sockets. The outermost
socket for every leg is the hip, then knee, then ankle. Make sure the yellow
wire is on the inside, and the brown one on the outside.



Attach the battery on the bottom of the printed circuit board. You can use a
rubber band or a double-sided adhesive tape. When connecting the battery, be
careful to connect the negative wire to the board's mass, and the positive one
to the switch (there is a small plus printed on the board).



If you want, you can tie the cables together to make the robot look better and
to avoid tangling. Make sure you leave enough loose cables for the legs to move
freely.



Adjustments
===========

You can edit the ``servos.ino`` file to adjust the trims for the servos. Edit
the ``ir.ino`` file to change the TV remote protocol, address and button codes,
to match yours. You can use the example code from the IRLremote library to read
the correct values for your remote. Edit the ``leg.ino`` file to change the
robot dimensions if the parts you used are different from what is described
here.

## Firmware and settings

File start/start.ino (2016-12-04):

#include "misc.h"
#include "servos.h"
#include "beep.h"
#include "battery.h"
#include "creep.h"
#include "leg.h"
#include "serialRemote.h"

#include <avr/sleep.h>

const int maxNumModes = 10;

const char* modeComment[maxNumModes];






int robot_mode = 2;


void setup() {
    modeComment[0] = "0: fold up";
    modeComment[1] = "1: Walk";
    modeComment[2] = "2: Stop";
    modeComment[3] = "3: Stand";
    
    battery_setup();
    servo_setup();
    //beep_setup();
    //ir_setup();
    serial_setup();
    //Serial.begin(9600);
}

void loop() {
    
    switch (robot_mode) {
        case 0: // Power off
            servo_fold();
//            servo_shutdown();
//            set_sleep_mode(SLEEP_MODE_PWR_DOWN);
//            sleep_enable();
//            sleep_mode();
//            while (1) {
//                delay(100);
//            }
            break;
        case 1:
            walk();
            break;
        case 2:  // stop
            servo_setup();
            break;
        case 3:
            servo_stand();
            break;
            
    }
    //ir_loop();
    //battery_loop();
    int modeIn = serial_loop();
    if (modeIn >=0 && modeIn < maxNumModes ){
        Serial.println(modeComment[modeIn]);
    }
    
    //Serial.println("test");
}

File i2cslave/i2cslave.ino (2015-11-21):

#include "servos.h"

#include <Wire.h>


const int SLAVE_ADDRESS = 0x04;


void setup() {
    Wire.begin(SLAVE_ADDRESS);
    Wire.onReceive(receiveEvent);
    servo_setup();
}


void loop() {
    delay(100);
}


void receiveEvent(int bytes) {
    union {
        byte bytes[4];
        float value;
    } float2bytes;
    unsigned int servo = Wire.read() | Wire.read() << 8;
    for (int j = 0; j < 4; ++j) {
        if (!Wire.available()) { return; }
        float2bytes.bytes[j] = Wire.read();
    }
    servo_move(servo, float2bytes.value);
}

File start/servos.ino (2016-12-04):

#include "misc.h"
#include "servos.h"
#include <Servo.h>

// Range of the servos.
#define SERVO_FREQ_MIN 600
#define SERVO_FREQ_MAX 2400

static const unsigned char SERVO_PINS[SERVOS] = {
// ankle, knee, hip

/* For Pro Micro
    14, 16, 10,     // front left
    A0, A1, A2,     // hind left
*/

    12, 11, 10,     // front left
    14, 15, 16,     // hind left
    6, 5, 4,        // hind right
    7, 8, 9         // front right
};
static const signed char SERVO_REVERSE[SERVOS] = {
// ankle, knee, hip
    -1, 1, 1,    // front left
    1, -1, -1,   // hind left
    -1, 1, 1,    // hind right
    1, -1, -1    // front right
};
static const signed char SERVO_TRIM[SERVOS] = {
// ankle, knee, hip
    -10, -5, -10,    // front left
    10, -5, -10,    // hind left
    0, 0, 10,    // hind right
    0, 0, 10     // front right
};
static Servo servos[SERVOS];

static const double HOME_POSITION[SERVOS] = {
// ankle, knee, hip
    0, 0, 0,    // front left
    0, 0, 0,    // hind left
    0, 0, 0,    // hind right
    0, 0, 0     // front right
};

static const double FOLD_POSITION[SERVOS] = {
// ankle, knee, hip
    -PI2,  PI2, -PI4,    // front left
    -PI2,  PI2, -PI4,    // hind left
    -PI2,  PI2, -PI4,    // hind right
    -PI2,  PI2, -PI4     // front right
};

static const double STAND_POSITION[SERVOS] = {
// ankle, knee, hip
    PI2,  -PI2, -PI4,    // front left
    PI2,  -PI2, -PI4,    // hind left
    PI2,  -PI2, -PI4,    // hind right
    PI2,  -PI2, -PI4     // front right
};


void servo_move(unsigned char servo, double rads) {
    // Move a servo to a position in radians between -PI/2 and PI/2.
    if (servo >= SERVOS) {
        return;
    }
    rads = rads * SERVO_REVERSE[servo] + PI2;
    while (rads > TAU) {
        rads -= TAU;
    }
    while (rads < 0) {
        rads += TAU;
    }
    int freq = (SERVO_FREQ_MAX -
                SERVO_FREQ_MIN) * rads / PI + SERVO_FREQ_MIN;
    freq = min(SERVO_FREQ_MAX,
               max(SERVO_FREQ_MIN,
                   freq + SERVO_TRIM[servo] * 10));
    servos[servo].writeMicroseconds(freq);
}

void servo_setup() {
    // Initialize all servos.
    // Start with hips.
    for (unsigned char servo = 2; servo < SERVOS; servo += 3) {
        servos[servo].attach(SERVO_PINS[servo],
                             SERVO_FREQ_MIN, SERVO_FREQ_MAX);
        servo_move(servo, HOME_POSITION[servo]);
        delay(150);
    }
    // Then ankles.
    for (unsigned char servo = 0; servo < SERVOS; servo += 3) {
        servos[servo].attach(SERVO_PINS[servo],
                             SERVO_FREQ_MIN, SERVO_FREQ_MAX);
        servo_move(servo, HOME_POSITION[servo]);
        delay(150);
    }
    // Finally knees.
    for (unsigned char servo = 1; servo < SERVOS; servo += 3) {
        servos[servo].attach(SERVO_PINS[servo],
                             SERVO_FREQ_MIN, SERVO_FREQ_MAX);
        servo_move(servo, HOME_POSITION[servo]);
        delay(150);
    }
}

void servo_shutdown() {
    // Power down all servos.
    for (unsigned char servo = 0; servo < SERVOS; ++servo) {
        servo_move(servo, FOLD_POSITION[servo]);
    }
    delay(500);
    for (unsigned char servo = 0; servo < SERVOS; ++servo) {
        servos[servo].detach();
    }
}

void servo_fold(){
    for (unsigned char servo = 0; servo < SERVOS; ++servo) {
        servo_move(servo, FOLD_POSITION[servo]);
    }
}

void servo_stand(){
    for (unsigned char servo = 0; servo < SERVOS; ++servo) {
        servo_move(servo, STAND_POSITION[servo]);
    }
}

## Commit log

2015-01-29 Init servos in sane order.
2015-01-30 Basic sketch of the creep gait (not working)
    [creep.ino]
2015-01-31 Tune the servo directions
2015-01-31 Remove debug prints
2015-01-31 Fix leg IK
2015-02-19 Finally fix orientation of servos, first proper creep
    [dice.fzz]
2015-02-20 Add scad files
    [dice.scad, parts.scad]
2015-02-21 More accurate scad model
    [dice.scad, parts.scad]
2015-02-21 Even more detail for the servo plugs
    [dice.scad, parts.scad]
2015-02-21 More accurate screws in scad
    [dice.scad, parts.scad]
2015-02-21 Images for all the assembly steps
    [dice.scad, parts.scad, step01.scad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]
2015-02-21 Assembly instructions
    [step01.scad]
2015-02-21 Add plans for dice2
    [dice.scad, dice2.fzz, dice2.scad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]
2015-02-21 Fix the hip servo orientation in scad files
    [dice.scad, step03.scad]
2015-02-21 Small tweaks of scad files
    [dice2.scad, parts.scad]
2015-02-22 Add more buttons
2015-02-23 Adjust servo trims
2015-02-28 Rename the project to Tote
    [pcb.fzz, pvb2.fzz]
2015-02-28 Rename in scad files
    [step01.scad, step02.scad, step03.scad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]
2015-02-28 Second version
    [gun.fzz, pcb.fzz, pcb2.fzz]
2015-03-19 Rename main.ino to start.ino, update the board
    [pcb.fzz, pcb2.fzz]
2015-03-21 Add a chapter about gaits
    [step01.scad, step02.scad, step03.scad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]
2015-03-21 Inverse kinematics
2015-03-29 Show all three possible leg orders
    [step05.scad, step06.scad]
2015-03-29 Add fourth leg order
    [step07.scad]
2015-04-13 Better info about soldering
2015-04-17 Add details to the scad model board
    [tote2.scad]
2015-04-17 Use the big servos in all scad files
    [pkubik.scad, step01.scad, step02.scad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]
2015-04-17 Show goldpins and re-generate assembly images
    [parts.scad, step01.scad, step03.scad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]
2015-04-17 re-generate main image
    [tote.scad]
2015-04-17 Update the BOM for the new version
2015-04-17 Add legs to the switch
    [parts.scad]
2015-04-18 Add version with pins and sockets
    [parts.scad, step01b.scad]
2015-04-25 Nicer labels on the pcb
    [pcb2.fzz]
2015-04-27 Move scad/ to doc/
    [parts.scad, pkubik.scad, step01.scad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]
2015-04-27 Generate scad images with a makefile
    [assembly01.scad, assembly01b.scad, assembly02.scad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]
2015-04-27 Add camera positions to makefile in scad
    [gait01.scad, gait02.scad, gait03.scad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]
2015-04-27 Add description of the Pro Mini to BOM
    [bom-arduino.scad, gait01.scad, gait02.scad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]
2015-05-01 More images for the parts descriptions
    [parts.scad]
2015-05-01 Tutorial -- soldering the pins
2015-05-01 The scad files
    [bom-pins.scad, bom-servos.scad, tutorial-pins.scad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]
2015-05-01 Nicer soldering iron
    [tutorial-solder.scad]
2015-05-02 Use shorter code for ir interrupt
    [ir.ino]
2015-05-02 3.3V version of Pro Mini
2015-05-03 Mode switching
2015-05-05 Update the pcb2 board
    [pcb2.fzz]
2015-05-05 Add links to dirtypcbs and gerber files
2015-05-07 Fix a bug with double-lowering legs
    [creep.ino]
2015-05-07 Move the legs faster in trot
2015-05-09 Add battery checking
2015-05-10 Shut the robot down on low battery
2015-05-10 Go into sleep mode on powerdown
2015-05-10 Switch off the led when powering off
2015-05-10 Automatically switch to trot gait when the speed is > 1.5
2015-05-10 Select the best leg order for the given direction
2015-05-31 Reworked assembly instructions, added photos
    [servos.ino]
2015-05-31 Add screenshot of the arduino ide
2015-05-31 Add pictures for connecting servos, battery and arranging cables
2015-06-02 Add a warning about soldering Pro Mini
2015-06-06 Add silkscreen image and copper fills to the pcb
    [pcb2.fzz]
2015-06-11 Add a makefile for the arduino sketch
2015-06-16 Mention the different pin layout for other boards than Pro Mini
2015-06-26 Fix the TV remote code.
    [pcb2.fzz]
2015-06-26 Bring back the old PCB
    [pcb2.fzz]
2015-06-26 New version of the PCB
    [pcb3.fzz]
2015-06-26 Add A6 and A7 pins for 5V Pro Mini
    [pcb3.fzz]
2015-06-26 Adjust and rearrange some traces
    [pcb3.fzz]
2015-06-30 Clean up the schematics in fritzing files
    [pcb2.fzz, pcb3.fzz]
2015-07-01 Fix traces in PCB2 board
    [pcb2.fzz]
2015-07-04 Small touches for PCB3
    [pcb3.fzz]
2015-07-06 Tweak the PCB3 board further
    [pcb3.fzz]
2015-07-06 Add servo horn image
2015-07-22 The buzzer is now on pin 13
    [ir.ino]
2015-07-23 First sketch of the version 4 of the PCB
    [pcb4.fzz]
2015-07-23 Update version 4 of the PCB
    [pcb4.fzz]
2015-07-23 More tweaks for the vrsion 4 pcb
    [pcb4.fzz]
2015-07-23 More tweaks for pcb4
    [pcb4.fzz]
2015-07-23 More small tweaks and alignment for the PCB v4
    [pcb4.fzz]
2015-08-14 Add instructions for version 4 of the PCB
2015-08-14 Remove irrelevant photos from v4 assembly
2015-08-14 Buzzer is now on pin 13
2015-08-28 Explain the initial position of the legs in version 4
2015-09-22 Add an rpi hat -- work in progress
    [pcb-pi.fzz]
2015-09-25 Small updates for the pcb4
    [pcb-pi.fzz, pcb4.fzz]
2015-09-26 README.rst edited online with Bitbucket
    [assembly01.scad, assembly01b.scad, assembly02.scad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]
2015-11-21 Add i2c servo driver firmware
    [pcb4.fzz]
2015-12-21 servos.ino edited, no need for min/max magic with constrain :)
2015-12-21 servos.ino code look
